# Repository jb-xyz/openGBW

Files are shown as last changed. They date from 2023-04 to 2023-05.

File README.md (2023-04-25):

# OpenGBW

This Project extends and adapts the original by Guillaume Besson

More info: https://besson.co/projects/coffee-grinder-smart-scale

This mod will add GBW functionality to basically any coffe grinder that can be started and stopped manually.

The included 3D Models are adapted to the Eureka Mignon XL, but the electronics can be used for any Scale.

-----------

### Differences to the original

- added a rotary encoder to select weight and navigate menus
- made everything user configurable without having to compile your custom firmware
- dynamically adjust the weight offset after each grind
- added relay for greater compatibility
- added different ways to activate the grinder
- added scale only mode

-----------

### Getting started

1) 3D print the included models for a Eureka Mignon XL or design your own
2) flash the firmware onto an ESP32
3) connect the display, relay, load cell and rotary encoder to the ESP32 according to the wiring instructions
4) go into the menu by pressing the button of the rotary encoder and set your initial offset. -2g is a good enough starting value for a Mignon XL
5) if you're using the Mignon's push button to activate the grinder set grinding mode to impulse. If you're connected directly to the motor relay use continuous.
6) if you only want to use the scale to check your weight when single dosing, set scale mode to scale only. This will not trigger any relay switching and start a timer when the weight begins to increase. If you'd like to build your own brew scale with timer, this is also the mode to use.
7) calibrate your load cell by placing a 100g weight on it and following the instructions in the menu
8) set your dosing cup weight
5) exit the menu, set your desired weight and place your empty dosing cup on the scale. The first grind might be off by a bit - the accuracy will increase with each grind as the scale auto adjusts the grinding offset

-----------

### Wiring

#### Load Cell

| Load Cell  | HX711 | ESP32  |
|---|---|---|
| black  | E-  | |
| red  | E+  | |
| green  | A+  | |
| white  | A-  | |
| | VCC  | VCC/3.3 |
| | GND  | GND |
| | SCK  | GPIO 18 |
| | DT  | GPIO 19|

#### Display

| Display | ESP32 |
|---|---|
| VCC | VCC/3.3 |
| GND | GND |
| SCL | GPIO 22 |
| SDA | GPIO 21 |

#### Relay

| Relay | ESP32 | Grinder |
|---|---|---|
| + | VCC/3.3 | |
| - | GND | |
| S | GPIO 33 | |
| Middle Screw Terminal | | push button |
| NO Screw Terminal | | push button |

#### Rotary Encoder

| Encoder | ESP32 |
|---|---|
| VCC/+ | VCC/3.3 |
| GND | GND |
| SW | GPIO 34 |
| DT | GPIO 23 |
| CLK | GPIO 32 |

-----------

### BOM

1x ESP32  
1x HX711 load cell amplifier  
1x 0.9" OLED Display  
1x KY-040 rotary encoder  
1x 500g load cell 60 x 15,8 x 6,7 https://www.amazon.de/gp/product/B019JO9BWK/ref=ppx_yo_dt_b_asin_title_o02_s00?ie=UTF8&psc=1  

various jumper cables  
a few WAGO or similar connectors

-----------

### 3D Files

You can find the 3D STL models on thangs.com

Eureka XL: https://thangs.com/designer/jbear-xyz/3d-model/Eureka%20Mignon%20XL%20OpenGBW%20scale%20addon-834667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

These _should_ fit any grinder in the Mignon line up as far as I can tell.

There's also STLs for a universal scale in the repo, though it is mostly meant as a starting off point to create your own. You can use the provided files, but you'll need to print an external enclosure for the ESP32, relay and any other components your setup might need.

### Todo:

- ~add option to change grind start/stop behaviour. Right now it pulses for 50ms, this works if its hooked up to the push button of a Eureka grinder. Other models might need constant input while grinding~ done
- add mounting options and cable routing channels to base
- more detailed instructions (with pictures!)
- other grinders?
- ???

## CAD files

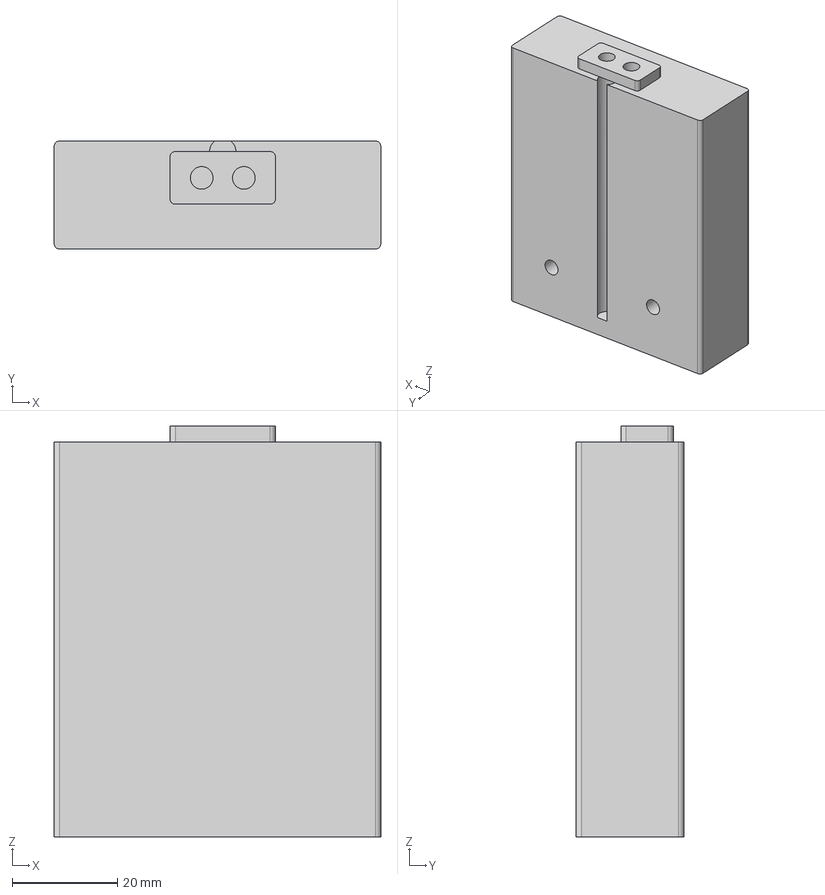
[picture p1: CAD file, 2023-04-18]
3D/Mignon XL/Scale Addon - Scale Body.step
62.0 x 20.5 x 78.0 mm

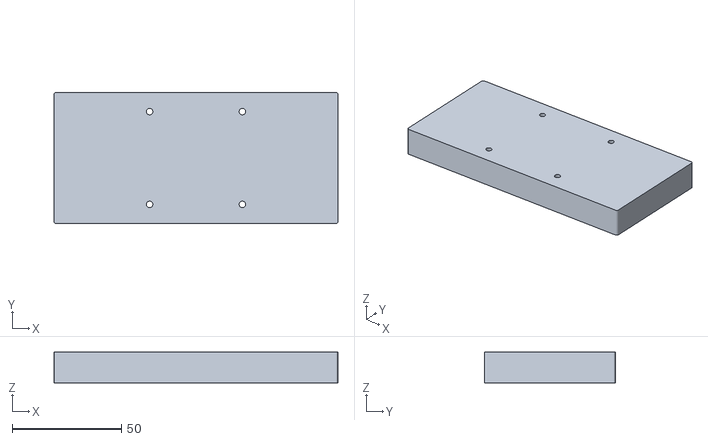
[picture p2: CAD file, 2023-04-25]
3D/Universal Scale/Universal Scale - Top.stl
130.0 x 60.0 x 14.0

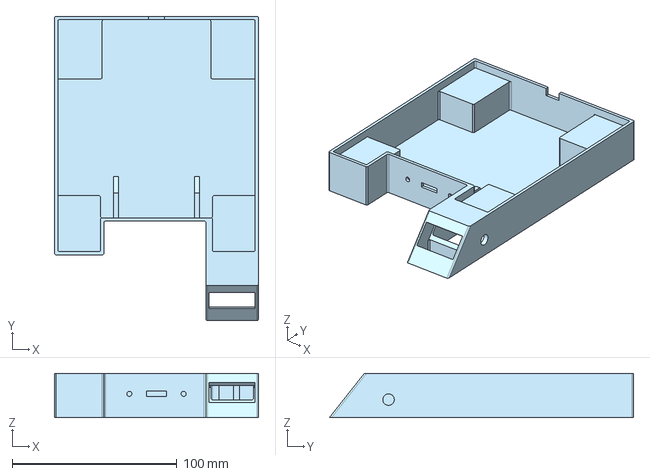
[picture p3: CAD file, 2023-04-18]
3D/Mignon XL/Scale Addon - Base.step
124.0 x 185.0 x 27.0 mm

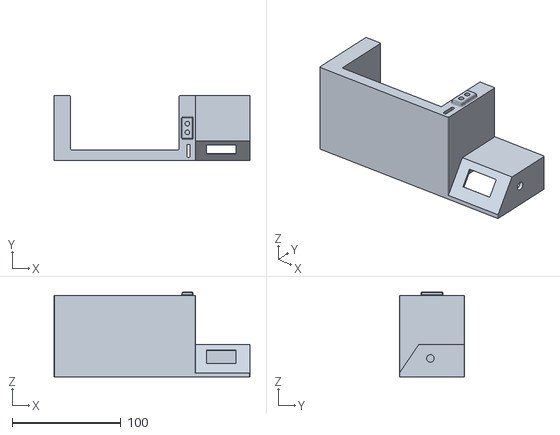
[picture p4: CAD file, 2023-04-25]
3D/Universal Scale/Universal Scale - Body.stl
180.0 x 60.0 x 78.0

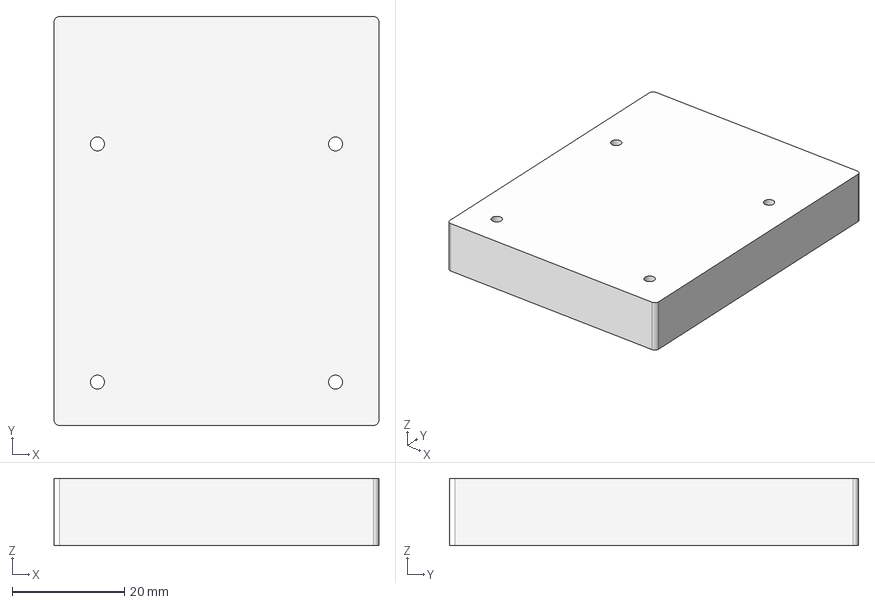
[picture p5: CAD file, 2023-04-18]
3D/Mignon XL/Scale Addon - Scale Top.step
58.0 x 73.0 x 12.0 mm

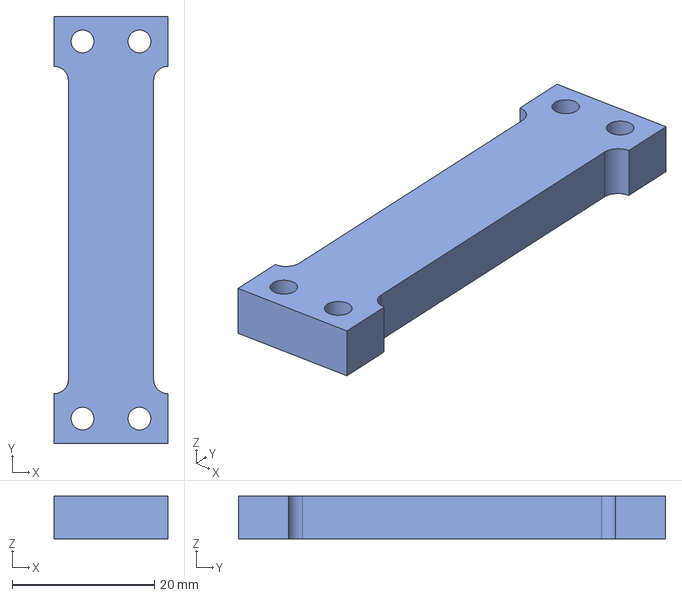
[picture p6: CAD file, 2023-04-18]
3D/Mignon XL/Scale Addon - Load Cell - DONT PRINT ONLY FOR REFERENCE.step
16.0 x 60.0 x 6.00 mm

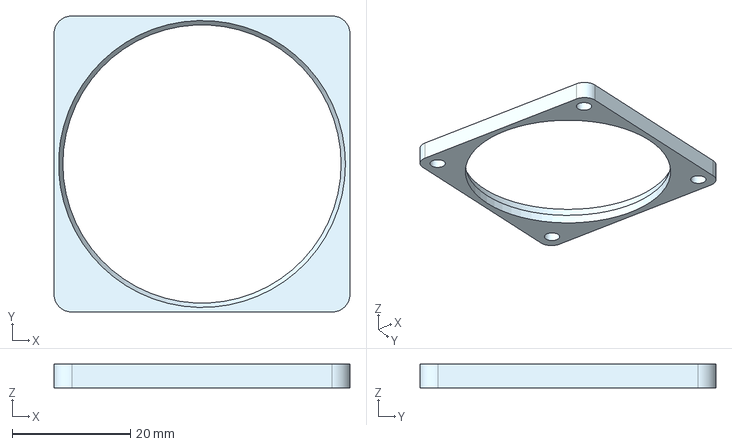
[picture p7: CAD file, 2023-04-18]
3D/Mignon XL/Scale Addon - Dosing cup Holder.step
50.0 x 50.0 x 4.00 mm

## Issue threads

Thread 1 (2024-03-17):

Using a 1kg load cell instead?

Geoffwithaj, 2024-03-17:
Hi, I'm just wondering what modifications might need to be made to use a 1kg load cell instead of the .5kg? Would that be sorted out during calibration?

jb-xyz, 2024-03-17:
Absolutely, calibration would take care of that.

I just went with the 500g one for accuracy

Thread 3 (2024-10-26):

Weight measurement not working

marvke-mautz, 2024-10-26:
I got a problem with the measurement of the weight.
Just after initializing the weight is "nang"

I checked the wiring and the connections several times and they are fine.
The resistance of the load cell and the is also fine. The voltage is changing by give it some load.
I replaced the hx711 boards to better ones.

Now i have no idea what i could check next. Maybe you can help me.

Thanks in advance!

Maggero, 2024-11-08:
Hey im sitting 1 week for now on this Project.... dont get the esp32 flashed can you maybe help me ? your comment is 2 weeks old hopefully i get some help =)

jb-xyz, 2024-11-09:
Hello, if you are using platform.io it has an inbuilt flash function, otherwise you can flash the binary using any esp32 flashing tool.

https://www.espressif.com/en/support/download/other-tools

here's espressif's tool, but you can also try any other

jb-xyz, 2024-11-09:
> marvke-mautz
> the display shows "grinding failed". The monitor in platformio shows "failed because weight too low"

this happens when the weight doesn't change enough. I hard coded a value that worked fine for my grinder and coffee, but it's definitely something i should make configurable in the next release. I'll probably have some spare time to work on it again in december.

marvke-mautz, 2024-11-13:
i have a mignon silenzio, which has much a slower grind rate than the mignon xl. so i had to change the values.

i use the setup everyday and i am very happy how reliable it works. thank you for your work!

also i shortened the 3d model "scale body" by 15mm in order to fit with the smaller migon silenzio form factor.

dimiepp, 2024-11-16:
> But now i have another problem. The grinder starts by placing the dosing cup on the scale and stops immediatly. the display shows "grinding failed". The monitor in platformio shows "failed because weight too low"
>
> EDIT: I did some adjustments in the code. Now it works! NICE!

Can you share the changes you made? Habe exactly the same issue

chinchean99, 2025-05-28:
Hi, may i know how you solve the "nang"?

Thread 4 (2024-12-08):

Need some help with my homemade grinder,  have a problem between my relay and the "continuous" mode..?

poulpor, 2024-12-08:
Hi,
I'm sorry to bother you but I do it as a last resort, because for weeks, I can't get around the problem I have while I try to do my own grinder, using a spare grinder pulled from an automatic coffee machine with ceramic burrs, some 3D printing and, obviously, your nice piece of software, OpenGBW!

I had to buy[ a relay, a very classic one, 3.3V](https://fr.aliexpress.com/item/1005005319972049.html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), to power on an AC 220V to DC 10-210V PWM Motor controller which drives the DC220V motor of the grinder. I suppose this part is not faulty because when I disconnect it, the relay acts the same.

So my problem is, when I select "Continuous" in Grinding Mode menu, the relay doesn't simply stays up but looks like it just rapidly goes up and down, based on the clicking sound you can ear in this [video](https://pics.pmchan.ovh/video/XWLf).
Secondly, the screen rapidly display Grinding failed and glitches during all the time the relay is going up and down.

The impulse setting works as intended and without glitches on the screen.

Did I do something wrong or is it a normal behavior?

I hope you'll be able to help me, it's driving me crazy, I first thought it was because of the motor emitting EMI, and moved all the esp32 parts away of it, but it didn't solve anything.

Thank you for your time and, again, for this nice project I'm trying to adapt since... too much time ^^;

matteohoeren, 2025-02-08:
@poulpor The clicking comes from the logic, that the scale wants to be reset by a higher weight than the dosing cup. This is defined in scale.hpp

#define GRINDING_FAILED_WEIGHT_TO_RESET 150

You want to set that higher than the weight of your portafilter.
I'm also having issues with this project, and i've fixed a couple for my setup, however the HX711 sensor seems to loose connection shortly after grinding started. No idea why atm, but looking into that.

Once you fixed the issue above, see the serial monitor WHY grinding fails. You might want to adjust the parameters that trigger a fail condition.
Hope that helps.

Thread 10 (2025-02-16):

nan after calibrating

Midti, 2025-02-16:
Hi, first of all thank you for sharing this great DIY project.

I have an issue:

Preface: I have used similar components as you except for a Live Mini Kit ESP32 Wroom. I am using the same IO ports on the ESP32 as you for the scale.

 I have everything up and running, but when I finish calibrating the scale with 100g it will now only display:
"nang", even when I try to calibrate with no weight on the scale to reset. The only way I seem to be able to clear the "nang" and get the scale showing numbers again is to completely wipe the ESP32, and then flash the code to it again, but whenever I try to calibrate it goes to "nang" and stays there.

*EDIT* This is the fault I see in the terminal when trying to calibrate with 100g:

Calibration Menu
[ 57017][E][Preferences.cpp:503] getBytesLength(): nvs_get_blob len fail: calibration NOT_FOUND
0.00

Any help would be greatly appreciated.

Midti, 2025-02-16:
I tried the feature additions from SyButter under pull requests, that works with calibration.

Closed 2025-02-16.

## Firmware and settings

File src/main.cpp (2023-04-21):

#include <Arduino.h>
#include <WiFi.h>
#include <PubSubClient.h>


#include "display.hpp"
#include "scale.hpp"

WiFiClient espClient;
PubSubClient client(espClient);

//wifi not used for now. Maybe OTA later
const char *ssid = "ssid"; // Change this to your WiFi SSID
const char *password = "pw"; // Change this to your WiFi password
long lastReconnectAttempt = 0;


void setup() {
  Serial.begin(115200);
  while(!Serial){delay(100);}

  
  setupDisplay();
  setupScale();

  Serial.println();
  Serial.println("******************************************************");
  // Serial.print("Connecting to ");
  // Serial.println(ssid);

  // WiFi.begin(ssid, password);

  // while (WiFi.status() != WL_CONNECTED) {
  //   delay(500);
  //   Serial.print(".");
  // }

  // Serial.println("");
  // Serial.println("WiFi connected");
  // Serial.println("IP address: ");
  // Serial.println(WiFi.localIP());
  // lastReconnectAttempt = 0;
  // client.setServer("192.168.1.201", 1883);
}

boolean reconnect() {
  if (client.connect("coffee-scale")) {
    // Once connected, publish an announcement...
    Serial.println("Connected to MQTT");
  }
  return client.connected();
}

void loop() {
  // if (!client.connected()) {
  //   long now = millis();
  //   if (now - lastReconnectAttempt > 5000) {
  //     lastReconnectAttempt = now;
  //     // Attempt to reconnect
  //     if (reconnect()) {
  //       lastReconnectAttempt = 0;
  //     }
  //   }
  // } else {
  //   client.loop();
  // }
  //rotary_loop();
  delay(1000);
}

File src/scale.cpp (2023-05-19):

#include "scale.hpp"
#include <MathBuffer.h>
#include <AiEsp32RotaryEncoder.h>
#include <Preferences.h>

HX711 loadcell;
SimpleKalmanFilter kalmanFilter(0.02, 0.02, 0.01);

Preferences preferences;


AiEsp32RotaryEncoder rotaryEncoder = AiEsp32RotaryEncoder(ROTARY_ENCODER_A_PIN, ROTARY_ENCODER_B_PIN, ROTARY_ENCODER_BUTTON_PIN, ROTARY_ENCODER_VCC_PIN, ROTARY_ENCODER_STEPS);

#define ABS(a) (((a) > 0) ? (a) : ((a) * -1))

TaskHandle_t ScaleTask;
TaskHandle_t ScaleStatusTask;

double scaleWeight = 0; //current weight
double setWeight = 0; //desired amount of coffee
double setCupWeight = 0; //cup weight set by user
double offset = 0; //stop x grams prios to set weight
bool scaleMode = false; //use as regular scale with timer if true
bool grindMode = false;  //false for impulse to start/stop grinding, true for continuous on while grinding
bool grinderActive = false; //needed for continuous mode
MathBuffer<double, 100> weightHistory;

unsigned long scaleLastUpdatedAt = 0;
unsigned long lastSignificantWeightChangeAt = 0;
unsigned long lastTareAt = 0; // if 0, should tare load cell, else represent when it was last tared
bool scaleReady = false;
int scaleStatus = STATUS_EMPTY;
double cupWeightEmpty = 0; //measured actual cup weight
unsigned long startedGrindingAt = 0;
unsigned long finishedGrindingAt = 0;
int encoderDir = 1;
bool greset = false;

bool newOffset = false;

int currentMenuItem = 0;
int currentSetting;
int encoderValue = 0;
int menuItemsCount = 7;
MenuItem menuItems[7] = {
    {1, false, "Cup weight", 1, &setCupWeight},
    {2, false, "Calibrate", 0},
    {3, false, "Offset", 0.1, &offset},
    {4, false, "Scale Mode", 0},
    {5, false, "Grinding Mode", 0},
    {6, false, "Exit", 0},
    {7, false, "Reset", 0}}; // structure is mostly useless for now, plan on making menu easier to customize later

void rotary_onButtonClick()
{
  static unsigned long lastTimePressed = 0;
  // ignore multiple press in that time milliseconds
  if (millis() - lastTimePressed < 500)
  {
    return;
  }
  if(scaleStatus == STATUS_EMPTY){
    scaleStatus = STATUS_IN_MENU;
    currentMenuItem = 0;
    rotaryEncoder.setAcceleration(0);
  }
  else if(scaleStatus == STATUS_IN_MENU){
    if(currentMenuItem == 5){
      scaleStatus = STATUS_EMPTY;
      rotaryEncoder.setAcceleration(100);
      Serial.println("Exited Menu");
    }
    else if (currentMenuItem == 2){
      scaleStatus = STATUS_IN_SUBMENU;
      currentSetting = 2;
      Serial.println("Offset Menu");
    }
    else if (currentMenuItem == 0)
    {
      scaleStatus = STATUS_IN_SUBMENU;
      currentSetting = 0;
      Serial.println("Cup Menu");
    }
    else if (currentMenuItem == 1)
    {
      scaleStatus = STATUS_IN_SUBMENU;
      currentSetting = 1;
      Serial.println("Calibration Menu");
    }
    else if (currentMenuItem == 3)
    {
      scaleStatus = STATUS_IN_SUBMENU;
      currentSetting = 3;
      Serial.println("Scale Mode Menu");
    }
    else if (currentMenuItem == 4)
    {
      scaleStatus = STATUS_IN_SUBMENU;
      currentSetting = 4;
      Serial.println("Grind Mode Menu");
    }
    else if (currentMenuItem == 6)
    {
      scaleStatus = STATUS_IN_SUBMENU;
      currentSetting = 6;
      greset = false;
      Serial.println("Reset Menu");
    }
  }
  else if(scaleStatus == STATUS_IN_SUBMENU){
    if(currentSetting == 2){

      preferences.begin("scale", false);
      preferences.putDouble("offset", offset);
      preferences.end();
      scaleStatus = STATUS_IN_MENU;
      currentSetting = -1;
    }
    else if (currentSetting == 0)
    {
      if(scaleWeight > 30){       //prevent accidental setting with no cup
        setCupWeight = scaleWeight;
        Serial.println(setCupWeight);
        
        preferences.begin("scale", false);
        preferences.putDouble("cup", setCupWeight);
        preferences.end();
        scaleStatus = STATUS_IN_MENU;
        currentSetting = -1;
      }
    }
    else if (currentSetting == 1)
    {
      preferences.begin("scale", false);
      double newCalibrationValue = preferences.getDouble("calibration", newCalibrationValue) * (scaleWeight / 100);
      Serial.println(newCalibrationValue);
      preferences.putDouble("calibration", newCalibrationValue);
      preferences.end();
      loadcell.set_scale(newCalibrationValue);
      scaleStatus = STATUS_IN_MENU;
      currentSetting = -1;
    }
    else if (currentSetting == 3)
    {
      preferences.begin("scale", false);
      preferences.putBool("scaleMode", scaleMode);
      preferences.end();
      scaleStatus = STATUS_IN_MENU;
      currentSetting = -1;
    }
    else if (currentSetting == 4)
    {
      preferences.begin("scale", false);
      preferences.putBool("grindMode", grindMode);
      preferences.end();
      scaleStatus = STATUS_IN_MENU;
      currentSetting = -1;
    }
    else if (currentSetting == 6)
    {
      if(greset){
        preferences.begin("scale", false);
        preferences.putDouble("calibration", (double)LOADCELL_SCALE_FACTOR);
        setWeight = (double)COFFEE_DOSE_WEIGHT;
        preferences.putDouble("setWeight", (double)COFFEE_DOSE_WEIGHT);
        offset = (double)COFFEE_DOSE_OFFSET;
        preferences.putDouble("offset", (double)COFFEE_DOSE_OFFSET);
        setCupWeight = (double)CUP_WEIGHT;
        preferences.putDouble("cup", (double)CUP_WEIGHT);
        scaleMode = false;
        preferences.putBool("scaleMode", false);
        grindMode = false;
        preferences.putBool("grindMode", false);

        loadcell.set_scale((double)LOADCELL_SCALE_FACTOR);
        preferences.end();
      }
      
      scaleStatus = STATUS_IN_MENU;
      currentSetting = -1;
    }
  }
}
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

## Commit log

2023-04-18 added 3d STEP files
    [Scale Addon - Base.step, Scale Addon - Dosing cup Holder.step, Scale Addon - Load Cell - DONT PRINT ONLY FOR REFERENCE.step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]
2023-04-25 added universal scale STLs
    [Scale Addon - Base.step, Scale Addon - Dosing cup Holder.step, Scale Addon - Load Cell - DONT PRINT ONLY FOR REFERENCE.step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]
2023-05-19 added reset menu + sanity checks
    [scale.cpp, scale.hpp]
